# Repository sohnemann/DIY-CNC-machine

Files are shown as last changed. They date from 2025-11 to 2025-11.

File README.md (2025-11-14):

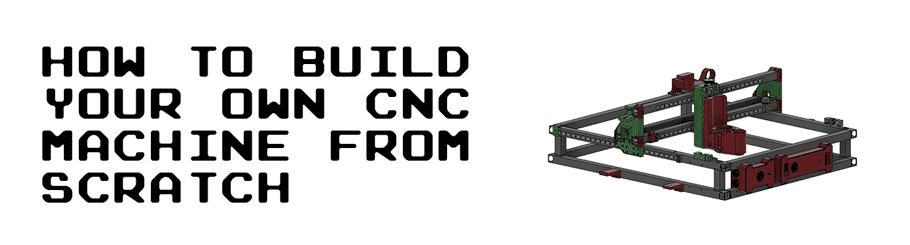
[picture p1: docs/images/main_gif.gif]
main_gif


This guide goes through all the steps to build your own CNC machine from scratch. It includes a complete bill of materials (BOM), STL/OBJ-files for all the 3d-printed parts and detailed instructions of how everything is assembled. It also includes instructions of how all the necessary open-source softwares are installed.

The guide is based on Ivan Miranada's design and is a complement to Ivan's Youtube-videos:

1. Original video: [https://www.youtube.com/watch?v=_atw3e0nIrg](https://www.youtube.com/watch?v=_atw3e0nIrg)
2. Updates with geared stepper motors etc: [https://www.youtube.com/watch?v=qpjf5D3WngY](https://www.youtube.com/watch?v=qpjf5D3WngY)
3. Updating to metal parts: [https://www.youtube.com/watch?v=RDnGvhdGFEY](https://www.youtube.com/watch?v=RDnGvhdGFEY)

If you have any questions, feel free to contact me on LinkedIn: [https://www.linkedin.com/in/max-fischer-92997281/](https://www.linkedin.com/in/max-fischer-92997281/) 

or

contact

cnc_top_gif

---

**Featured on**

* Hackernews (#2): [https://news.ycombinator.com/item?id=29096954](https://news.ycombinator.com/item?id=29096954)
* Console open-source newsletter: [https://console.substack.com/p/console-83](https://console.substack.com/p/console-83)
* Hackaday's blog: [https://hackaday.com/2021/11/05/diy-cnc-uses-lots-of-3d-printed-parts/](https://hackaday.com/2021/11/05/diy-cnc-uses-lots-of-3d-printed-parts/)
* Hackaday's podcast (~25:30): [https://open.spotify.com/episode/2YuxrVAgbQvVTjcUljJ3rj?si=lkp1L061R7ix6WkA7s1ieA](https://open.spotify.com/episode/2YuxrVAgbQvVTjcUljJ3rj?si=lkp1L061R7ix6WkA7s1ieA)
* Arduino's official blog: [https://blog.arduino.cc/2021/11/03/learn-how-to-build-your-own-massive-3d-printed-cnc-router/](https://blog.arduino.cc/2021/11/03/learn-how-to-build-your-own-massive-3d-printed-cnc-router/)
* Weekly robotics newsletter: [https://weeklyrobotics.com/weekly-robotics-168](https://weeklyrobotics.com/weekly-robotics-168)

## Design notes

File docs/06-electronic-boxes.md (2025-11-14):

# Electronic boxes

Two electronic boxes were attached to the front side of the CNC machine, a large box to encapsulate the power supply and a small box to encapsulate the Arduino and the CNC shield.

## Small electronic box

The small electronic box consisted of 4 parts (**P02**, **P04**, **P13**, **P15**). The two middle parts were clamped together on the front-left side of the frame, closest to the Y-axis cable chain. A finger was used to feel that the two parts were perfectly lined up.

Make sure to have enought space on the left side of the box for the all the stepper motor wires, end-stop wires and router power cable to enter the box (the vertical beam might block if you attach it too far to the left). Also make sure that the two holes are pointing to the left.

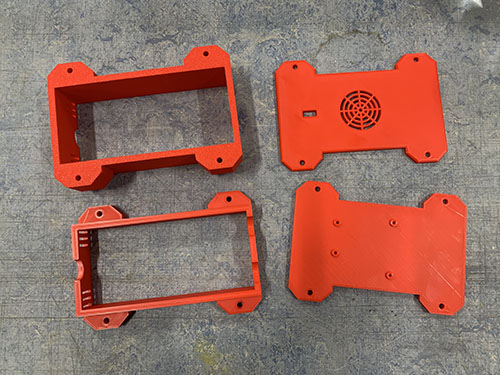
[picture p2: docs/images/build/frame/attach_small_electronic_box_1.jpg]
attach_small_electronic_box_1


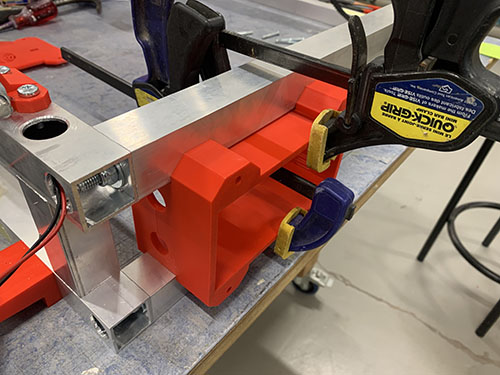
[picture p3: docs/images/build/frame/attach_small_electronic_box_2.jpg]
attach_small_electronic_box_2


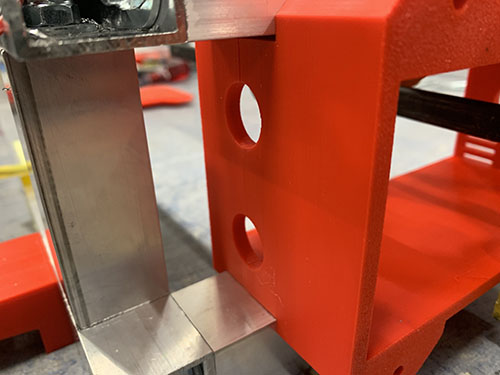
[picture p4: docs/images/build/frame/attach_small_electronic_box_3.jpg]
attach_small_electronic_box_3


The front-middle part (**P13**) was attached first. A small 2 mm drill was used to make indentations at the center of the holes. Cutting fluid was applied and a 3 mm drill was used to drill the holes, followed by a M4 drill tap. The front-middle and front part was then attached to the frame using 4x 40mm M4 screws (**S11**).

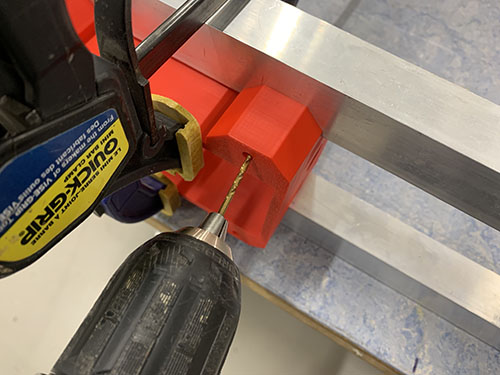
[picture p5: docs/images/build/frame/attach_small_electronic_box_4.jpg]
attach_small_electronic_box_4


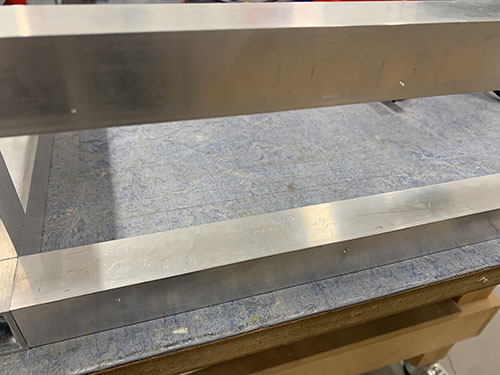
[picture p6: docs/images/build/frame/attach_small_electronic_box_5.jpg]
attach_small_electronic_box_5


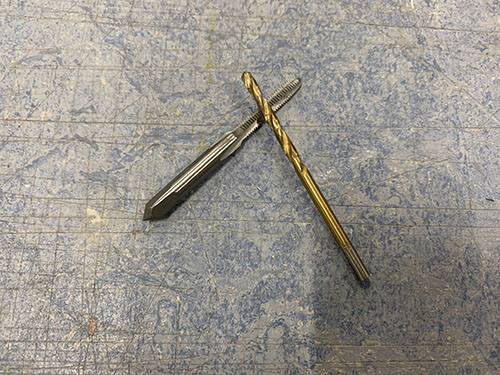
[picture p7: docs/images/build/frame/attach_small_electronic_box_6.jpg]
attach_small_electronic_box_6


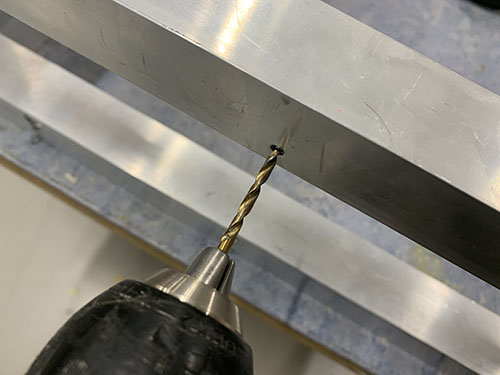
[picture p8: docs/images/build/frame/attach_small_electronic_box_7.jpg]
attach_small_electronic_box_7


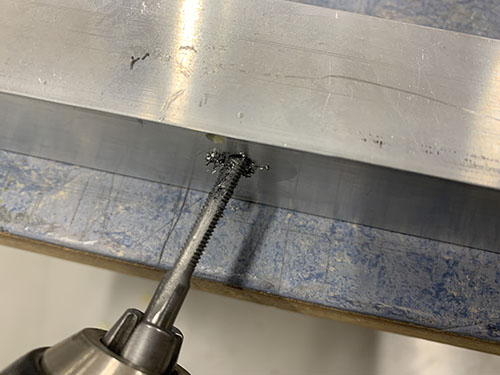
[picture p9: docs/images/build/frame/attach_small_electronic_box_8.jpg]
attach_small_electronic_box_8


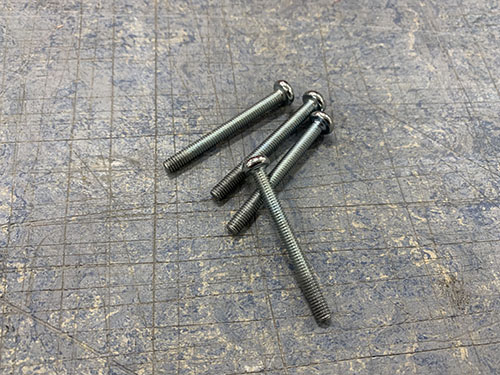
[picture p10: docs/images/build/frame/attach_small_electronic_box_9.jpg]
attach_small_electronic_box_9


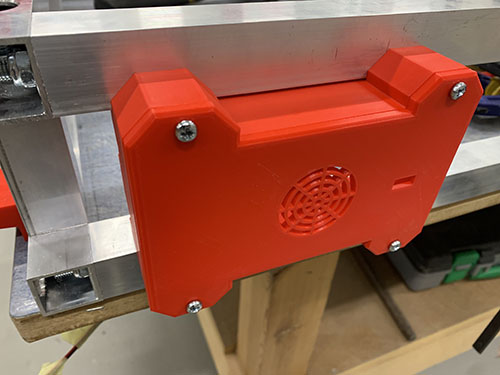
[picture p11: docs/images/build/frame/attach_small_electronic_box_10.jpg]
attach_small_electronic_box_10


To attach the back-middle part (**P02**), the whole CNC machine had to be pushed partly over the edge of the working table to be able to drill on the inside of the frame. The machine was firmly clamped to the table.

The back-middle part was again clamped to the frame and aligned with the now attached front-middle part. A small 2 mm drill was used to make indentations at the center of the holes. Cutting fluid was applied and a 3 mm drill was used to drill the holes, followed by a M4 drill tap. The back-middle and back part was then attached to the frame using 4x 25mm M4 screws (**S10**).

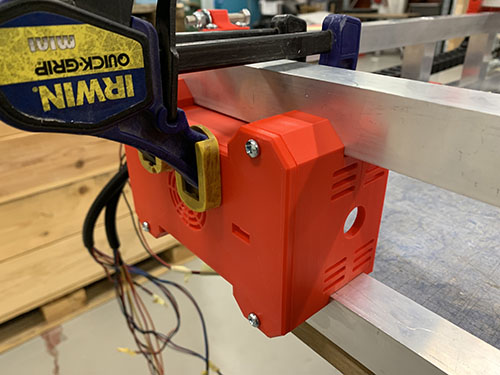
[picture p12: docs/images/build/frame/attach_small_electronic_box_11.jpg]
attach_small_electronic_box_11


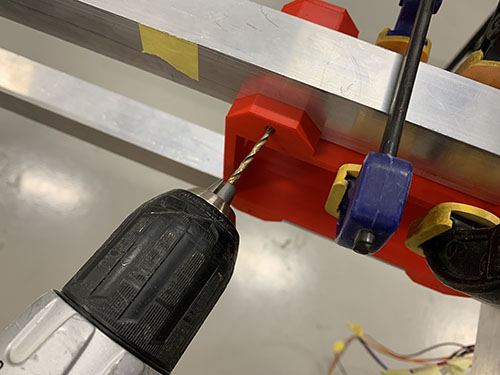
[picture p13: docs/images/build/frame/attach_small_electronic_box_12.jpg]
attach_small_electronic_box_12


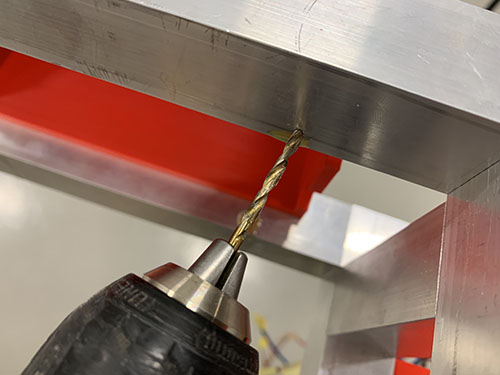
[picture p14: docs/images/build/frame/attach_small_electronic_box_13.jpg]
attach_small_electronic_box_13


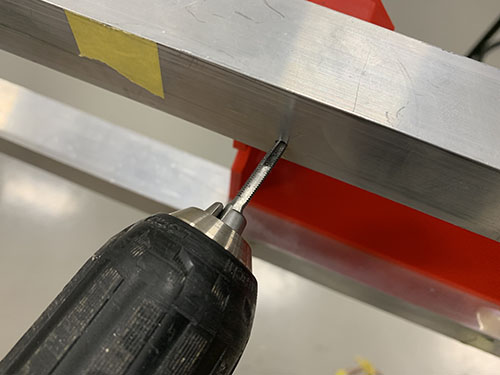
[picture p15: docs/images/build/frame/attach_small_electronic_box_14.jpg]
attach_small_electronic_box_14


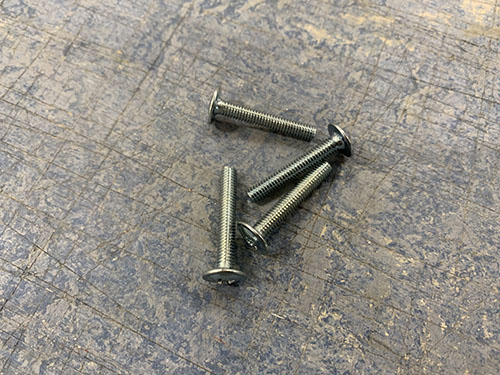
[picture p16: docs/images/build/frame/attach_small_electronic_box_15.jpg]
attach_small_electronic_box_15


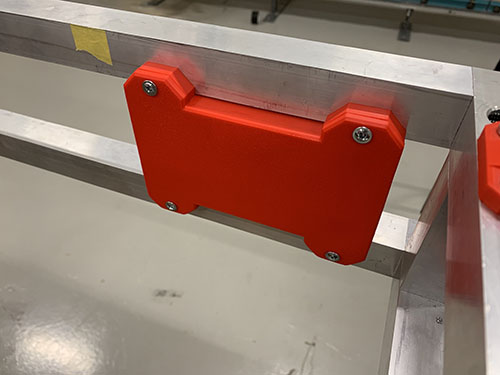
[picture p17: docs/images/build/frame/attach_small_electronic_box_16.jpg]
attach_small_electronic_box_16


## Large electronic box

As the small box, the large electronic box consisted of 4 parts (**P01**, **P03**, **P12**, **P14**). The two middle parts were clamped together to the right of the small box. A finger was used to feel that the two parts were perfectly lined up. 

Make sure that the hole is pointing to the left.

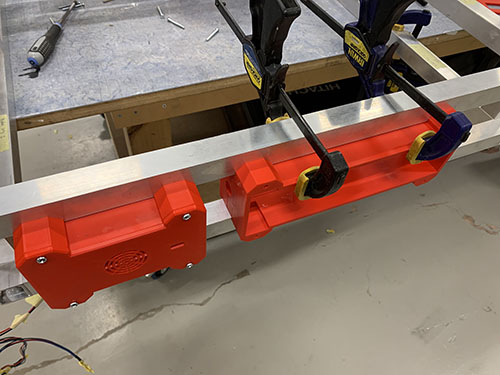
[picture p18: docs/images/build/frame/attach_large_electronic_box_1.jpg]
attach_large_electronic_box_1


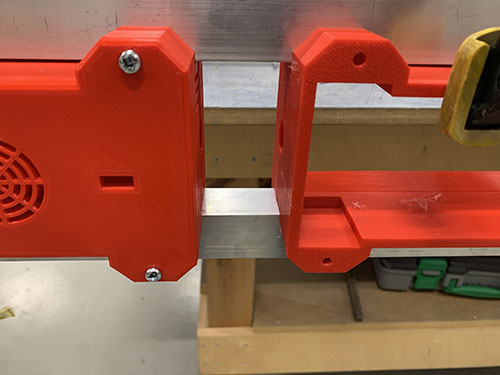
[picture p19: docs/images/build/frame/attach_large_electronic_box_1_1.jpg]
attach_large_electronic_box_1_1


The front-middle part (**P12**) was attached first. A small 2 mm drill was used to make indentations at the center of the holes. Cutting fluid was applied and a 3 mm drill was used to drill the holes, followed by a M4 drill tap. The front-middle and front part was then attached to the frame using 4x 40mm M4 screws (**S11**).

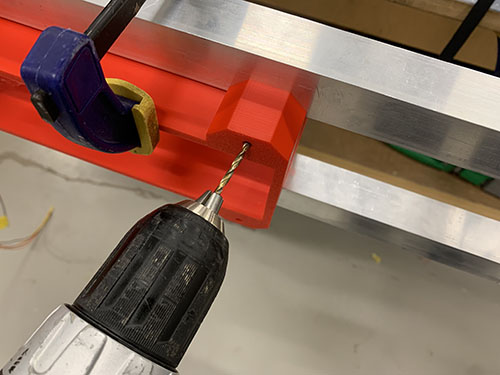
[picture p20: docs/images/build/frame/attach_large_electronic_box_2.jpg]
attach_large_electronic_box_2


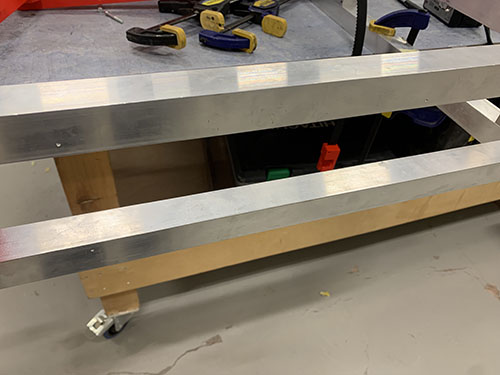
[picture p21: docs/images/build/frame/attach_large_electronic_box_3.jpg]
attach_large_electronic_box_3


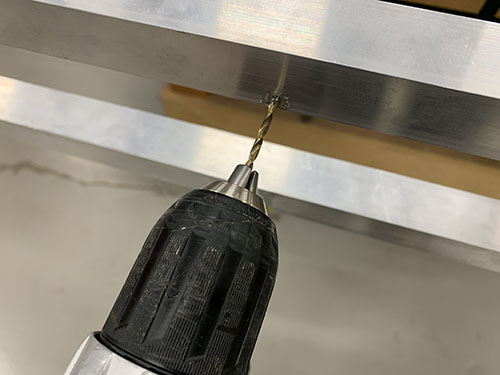
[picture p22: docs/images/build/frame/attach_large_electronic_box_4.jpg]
attach_large_electronic_box_4


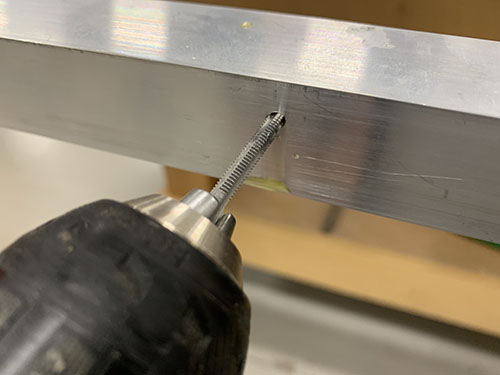
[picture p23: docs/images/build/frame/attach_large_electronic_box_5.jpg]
attach_large_electronic_box_5


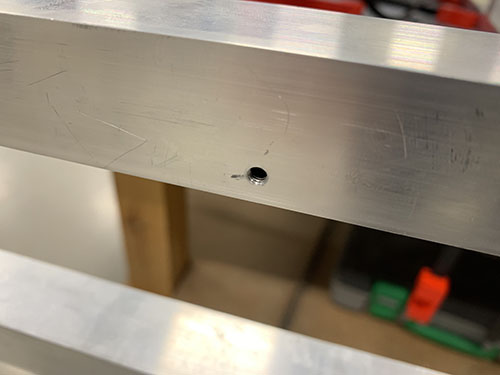
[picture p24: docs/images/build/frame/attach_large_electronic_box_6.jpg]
attach_large_electronic_box_6


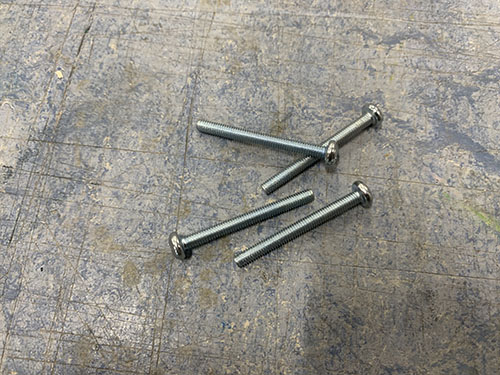
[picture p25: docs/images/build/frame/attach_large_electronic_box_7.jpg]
attach_large_electronic_box_7


attach_large_electronic_box_8

To attach the back-middle part (**P01**), the whole CNC machine had to be pushed partly over the edge of the working table to be able to drill on the inside of the frame. The machine was firmly clamped to the table.

The back-middle part was again clamped to the frame and aligned with the now attached front-middle part. A small 2 mm drill was used to make indentations at the center of the holes. Cutting fluid was applied and a 3 mm drill was used to drill the holes, followed by a M4 drill tap. The back-middle and back part was then attached to the frame using 4x 25mm M4 screws (**S10**).

attach_large_electronic_box_9

attach_large_electronic_box_10

attach_large_electronic_box_11

attach_large_electronic_box_12

attach_large_electronic_box_13

attach_large_electronic_box_14

attach_large_electronic_box_15

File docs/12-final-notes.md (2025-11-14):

# Final notes
I have a couple of things I want to improve with this build:

* [ ] Build a wasteboard using wasteboard clamps
* [x] Design a dust shoe

cnc_top_gif

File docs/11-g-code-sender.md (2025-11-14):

# G-Code sender

To be able to send G-Code instructions from the computer to `grbl` on the Arduino, a G-Code sender is needed. `grbl's` official list of recommended G-Code senders can be found here: [https://github.com/gnea/grbl/wiki/Using-Grbl](https://github.com/gnea/grbl/wiki/Using-Grbl) (Sep 26, 2021)

## Install G-Code sender

In this project a G-code sender called `Universal G-Code Sender (UGS)` was used. The program was downloaded from UGS's official website and the instructions were followed: 

[https://winder.github.io/ugs_website/download/](https://winder.github.io/ugs_website/download/)

After starting the program, you should see something like this:

gcode_sender_1

## Connect G-Code sender to GRBL

To let UGS know where to connect to, the correct firmware (GRBL) and serial port (cu.usbmodem\<NUMBER>) were chosen. If you can't find the correct serial port, click the spinning arrows to refresh the ports.

gcode_sender_2

gcode_sender_3

UGS was then connected to the Arduino by clicking on plug/socket icon in the top left corner. If the connection succeeds, you should see the plug/socket icon turn orange and the GRBL configuration outputted in the console.

gcode_sender_4

gcode_sender_5

## Adjust GRBL configuration

The GRBL configuration enables you to adjust important settings, such as the maximum mm/min rates for different axes and if the end-stops should be used. A full description of all settings can be found here:

[https://github.com/gnea/grbl/blob/master/doc/markdown/settings.md](https://github.com/gnea/grbl/blob/master/doc/markdown/settings.md) (Sep 26, 2021)

To update a setting, the new setting is inputted into the console command line, e.g.: `$21 = 1` to enable end-stops/hard limits. A confirmation that the setting is changed is then outputted in the console.

gcode_sender_6

### Enable end-stops/hard limits

The end-stops/hard limits were enabled by updating the following setting:

`$21 = 0` -> `$21 = 1`

To test that the end-stops were working properly, each end-stop was tested by manually triggering it with a finger. After triggering, an alarm should be raised in UGS.

gcode_sender_7

gcode_sender_8

After the alarm was triggered, UGS was reset by clicking `Soft reset` and `Unlock`.

gcode_sender_9

### Calculate and set travel resolutions

The most important settings to adjust is the X-axis, Y-axis and Z-axis travel resolutions. These settings tells GRBL how many steps it should take to move one millimeter. The travel resolution depends on the stepper motor's steps per revolution, the microstepping, the teeth spacing and the number of teeth on the timing pulley(s).

The following equation was used to calculate the travel resolution (steps/mm) for each stepper:

gcode_sender_10

In this project, this is how the travel resolutions were calculated:

| Stepper motor | Microstepping | Step angle | Steps per revolution | Teeth spacing | Number of teeth - Pulley 1 | Number of teeth - Pulley 2 | Travel resolution |
|---|---|---|---|---|---|---|---|
| X-axis | 16 | 0.094 deg  | 360/0.094 = 3829.7872 steps | 5 mm (HTD**5**M) | 12 | 1 (used when no pulley 2)  | **(16\*3829.7872)/(5\*12/1) = 1021.277** |
| Y-axis (1) | 16 | 0.094 deg  | 360/0.094 = 3829.7872 steps | 5 mm (HTD**5**M) | 12 | 1 (used when no pulley 2)  | **(16\*3829.7872)/(5\*12/1) = 1021.277** |
| Y-axis (2) | 16 | 0.094 deg  | 360/0.094 = 3829.7872 steps | 5 mm (HTD**5**M) | 12 | 1 (used when no pulley 2)  | **(16\*3829.7872)/(5\*12/1) = 1021.277** |
| Z-axis | 16 | 1.8 deg | 360/1.8 = 200 steps | 8 mm (acme rod)  | 16 | 60 | **(16\*200)/(8\*16/60) = 1500** |

The travel resolutions were updated:

* X-axis travel resolution: `$100=250.000` -> `$100 = 1021.277`
* Y-axis travel resolution: `$101=250.000` -> `$101 = 1021.277`
* Z-axis travel resolution: `$102=250.000` -> `$102 = 1500.000`

The calculated travel resolutions were validated by moving each axis 10 mm in UGS and measuring the actual distance moved.

gcode_sender_11

gcode_sender_12

gcode_sender_13

### Other configurations

The homing cycle is when the CNC machine automatically moves all axises to it's limits to home itself before starting the job. I disabled this as I will manually jog the router to it's position:

`$22 = 1` -> `$22 = 0`

The X-axis and Y-axis minimum rates were increased to 1000:

* X-axis maximum rate: `$110=500.000` -> `$110 = 1000.000`
* Y-axis maximum rate: `$111=500.000` -> `$111 = 1000.000`

The X-axis and Y-axis maximum travel were increased to 500:

* X-axis maximum travel: `$130=200.000` -> `$130 = 500.000`
* Y-axis maximum travel: `$131=200.000` -> `$131 = 500.000`

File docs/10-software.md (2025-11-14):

# Software

## Install CNC software (grbl) on Arduino Uno

The software used in this project to control the CNC machine is called `grbl`. It's an open source and high performance g-code-parser and CNC milling controller that can run on a straight Arduino Uno. To be able to install the software on the Arduino, an external computer was needed.

## Install Arduino Software (IDE)
To be able to install `grbl` on the Arduino, `Arduino Software (IDE)` was installed on the computer. This program is used to upload code to the Arduino. The program was downloaded from Arduino's official website and the instructions were followed: 

[https://www.arduino.cc/en/software](https://www.arduino.cc/en/software)

After starting the program, you should see something like this:

install_software_1

## Install GRBL
After installing the Arduino Software, the latest stable version of `grbl` was downloaded (as zip-format) from their official GitHub release page: 

[https://github.com/gnea/grbl/releases](https://github.com/gnea/grbl/releases)

After unzipping the file, you should see something similar to this in the folder:

install_software_2

Before `grbl` was loaded into the `Arduino Software (IDE)`, a minor adjustment had to be done to `grbl's` config file, `config.h`. The reason for this was because when `gbrl` released v1.1, it changed the pin used by the Z end-stops. If this wasn't done, the Z end-stops wouldn't be recognized by `grbl`. To tell `grbl` that the old way of accessing the Z end-stops should be used, a specific variable in the `config.h` was commented out. 

The config `grbl/config.h` was opened in a text editor and the line were the variable `VARIABLE_SPINDLE` is set was commented out by adding two slashes (//) at the beginning of the line (see the last line):

```
// Enables variable spindle output voltage for different RPM values. On the Arduino Uno, the spindle
// enable pin will output 5V for maximum RPM with 256 intermediate levels and 0V when disabled.
// NOTE: IMPORTANT for Arduino Unos! When enabled, the Z-limit pin D11 and spindle enable pin D12 switch!
// The hardware PWM output on pin D11 is required for variable spindle output voltages.
// #define VARIABLE_SPINDLE // <-- THIS SHOULD BE COMMENTED OUT!!
```

The updated `config.h` was saved.

The `Arduino Software (IDE)` was then launched and the `Sketch > Include Library > Add .ZIP Library...` menu alternative was clicked:

install_software_3

You should see a pop-up similar to this:

install_software_4

The unzipped `grbl` directory was opened and the folder `grbl` was chosen. After choosing the folder, a text below the editor appeared stating `Library added to your libraries. Check "Include library" menu`.

A USB cable was connected to the USB connection on the small electronic box.

Next, connect the Arduino to your computer.

install_software_5

To let the IDE know where to upload the software, the correct serial port and board were chosen. The serial port was set under `Tools > Port > SOMETHINGSOMETHING (Arduino Uno)`. 

```
If you have trouble finding the correct port, you might need to install 
CH340 drivers. It might occurr if you're using an Arduino clone. Look at
this resource for more info: 
https://learn.sparkfun.com/tutorials/how-to-install-ch340-drivers/all
```

install_software_8

The board was set under `Tools > Board > Arduino Uno`.

install_software_8_1

To test if the correct board and serial port were chosen, the template code (default code available when launching the IDE) was compiled by clicking on the check mark in the top left corner. When the compiling was done, the right-pointing arrow was clicked to upload the code to the Arduino. If successfull, you should see a text saying `Done uploading` below the editor.

install_software_9

install_software_10

The IDE was now ready to upload `grbl` to the Arduino. This was done by clicking `File > Open` in the top menu:

install_software_11

In the pop-up window, the downloaded folder was found and the following file  `grbl/examples/grblUpload/grblUpload.ino` was opened.

install_software_12

A new pop-up was opened and the `grbl` code was compile by clicking on the check mark. When done, the compiled code was uploaded to the Arduino by clicking on the right-pointing arrow. `grbl` was now installed on the Arduino!

install_software_13

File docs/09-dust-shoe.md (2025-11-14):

# Dust shoe

The purpose of a dust shoe is to collect the dust generated by the CNC machine. Ivan's original dust shoe didn't fit my router, thus I designed a new dust shoe using a brush.

To not have to reprint the router bracket, I manually cut of the blocking piece from it. The STL/OBJ router bracket file in this repo is redesigned and updated, so no manual cutting should be needed.

The brush slot at the bottom of the vaccum funnel (**P34**) was measured and the brush (**O27**) was cut at an appropriate length. The brush was then inserted into the slot. As the fit was very tight, no glue was needed.

dust_shoe_1

dust_shoe_2

dust_shoe_3

dust_shoe_4

The vaccum funnel (**P34**) was placed next to the router bracket (**P24**) and a pen was used to indicate how much of the router bracket that was to be removed.

dust_shoe_5

dust_shoe_6

A hand-held Fein multitool was used to remove the blocking piece from the router bracket. A sand paper was used to smooth out the edges.

dust_shoe_7

dust_shoe_8

dust_shoe_9

dust_shoe_10

The vaccum funnel was then attached to the router bracket and a scissor was used to cut the brush at an appropriate length.

dust_shoe_11

1x 80 mm M5 screw (**S17**) and 1x M5 nut (**N02**) was used to lock the vaccum funnel in place.

dust_shoe_14

dust_shoe_15

dust_shoe_16

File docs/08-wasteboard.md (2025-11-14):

# Wasteboard

## Cut out wasteboard

The length and width of the CNC was measured and a 12 mm plywood (**O26**) was cut out using a vertical panel saw. If you don't have a vertical panel saw, a jigsaw or a circular saw works as well.

wasteboard_1

wasteboard_2

wasteboard_3

## Attach wasteboard to CNC

The wasteboard was placed underneath the CNC machine. 7x 3d-printed wasteboard brackets (**P37**), 14x 3.5x20mm screws (**S01**) and 14x (15mm x 5mm x 1mm) washers (**W02**) were used to to keep the wasteboard in place.

wasteboard_4

wasteboard_5

wasteboard_7

wasteboard_6

wasteboard_8

wasteboard_9

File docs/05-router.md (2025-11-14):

# Router

## Attach router to carriage

A Makita RT0700CJ (**E20**) trimming router was used as I was not able to get my hands on the Makita RT0700C that Ivan is using. To my knowledge, the RT0700CJ is just an upgraded European version of the RT0700C, with the same dimensions.

The trimming router was locked in place by using the router bracket (**P24**), 4x 40mm M5 screws (**S13**), 4x M5 nuts (**N02**) and 4x (10mm x 5mm x 1mm) washers (**W01**).

attach_router_to_carriage_1

attach_router_to_carriage_2

attach_router_to_carriage_3

attach_router_to_carriage_4

attach_router_to_carriage_6

attach_router_to_carriage_7

## Router cable management

**NOTE: THIS PART INCLUDES WIRING OF HIGH VOLTAGE ELECTRICITY THAT CAN BE LETHAL IF NOT DONE PROPERLY. THE COLORS OF THE CABLES CAN VARY DEPENDING ON REGION/COUNTRY AND YOUR COMPONENTS/PINOUT NUMBERS MIGHT LOOK DIFFERENT. BEFORE YOU CONNECT THE POWER CORD TO THE POWER OUTLET, YOU MUST CONSULT WITH A LICENSED ELECTRICIAN TO MAKE SURE THAT EVERYTHING IS PROPERLY WIRED AND THAT IT IS IN LINE WITH YOUR LOCAL LEGISLATIONS.**

To be able to easily replace the trimming router in the future, a power plug (**E04**) and socket were added (**E05**).

router_cable_management_23

First, the router's power cord was cut and stripped at an appropriate length to reach behind the X-axis cable chain mount. A flexible conduit (**O13**) was cut out at an appropriate length and the power cord closest to the router was inserted into the conduit. The end of the power cord and the inside wires were then stripped and twisted.

router_cable_management_1

router_cable_management_2

router_cable_management_3

The power plug was opened up and the wires were connected. The built-in strain relief was then tightened around the cable before the plug was closed again.

router_cable_management_4

router_cable_management_5

router_cable_management_6

router_cable_management_7

router_cable_management_8

The rest of the power cord was inserted through the Y-axis cable chain, around the left side plate (under the cable tie) and through the X-axis cable chain. Getting the power cord through the X-axis cable chain was quite tricky due to the friction of the rubber cable. A cable tie (**O11**) was therefore attached to the top of the cable and used to pull the cable through the cable chain.

router_cable_management_9

router_cable_management_10

router_cable_management_11

router_cable_management_12

router_cable_management_13

router_cable_management_14

router_cable_management_15

The power cord was pulled through the cable chains and adjusted to an appropriate length to reach behind the X-axis cable chain mount. The end of the cable and the inside wires were then stripped and twisted.

router_cable_management_17

router_cable_management_19

The power socket was opened and the wires were attached to the terminals inside. The built-in strain relief was then tightened around the cable before the socket was closed again.

router_cable_management_16

router_cable_management_18

router_cable_management_20

router_cable_management_21

router_cable_management_22

The plug and socket were connected and strapped to the back of the X-axis cable chain mount using cable ties (**O11**). The flexible conduit with the router power cord inside was strapped to the stepper motor flexible conduit using cable ties (**O11**). Make sure that it doesn't touch and drag along the upper bridge beam.

router_cable_management_23

router_cable_management_24

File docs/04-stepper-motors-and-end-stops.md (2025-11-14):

# Stepper motors and end-stops

## Extend stepper motor wires

All 4 stepper motors (2x Y-axis, 1x X-axis and 1x Z-axis) get their power and movement instructions from the Arduino + CNC shield that in a later step will be attached in the small electronic box. Therefore, the stepper motor cables needed to be extended to reach through the cable chains all the way to the front of the machine, where the small electronic box will be located.

AWG22 cables (**E08**) of matching colors were used when increasing the length of the stepper motor cables. The same process was used for all the motors:

1. The amount of wires needed to reach all the way to the electronic box was approximated and cut. Make sure to have an extra ~300 mm wire from the point where the wires exits the Y-axis cable chain, as this will be needed to reach the small electronic box.
2. The ends of the original stepper wires and the extra AWG22 wires were stripped using a wire stripper.
3. The colors of the original stepper wires and the extra AWG22 wires were matched up and the stripped ends of the wires were twisted around each other.
4. The twisted wires where then locked in a steady position by a "third hand".
5. Soldering grease was applied to the twisted wires and the wires were soldered together.
6. 4 shrinking tubes (one per cable) were shrunk around the now soldered twisted wires, covering the soldering.
7. A handful of larger shrinking tubes were shrunk around all 4 wires to keep them together.
8. Finally, the wires were marked using tape and a penn, indicating which stepper motor the wires belonged to. This is important as it will help a lot later on, when the stepper motors are connected to the Arduino.

### Y-axis 1

The extended wires of the first Y-axis stepper motor were cut at a length so that they reached through the lower front bridge beam (see red arrow on the next image) and through the Y-axis cable chain going to the front of the CNC machine.

solder_steppers_y_axis_1

solder_steppers_y_axis_2

solder_steppers_y_axis_3

solder_steppers_y_axis_4

solder_steppers_y_axis_5

solder_steppers_y_axis_6

solder_steppers_y_axis_7

solder_steppers_y_axis_8

solder_steppers_y_axis_9

solder_steppers_y_axis_10

solder_steppers_y_axis_10_1

### Y-axis 2

The extended wires of the second Y-axis stepper motor were cut at a length so that they reached through the Y-axis cable chain going to the front of the CNC machine.

solder_steppers_y_axis_11

solder_steppers_y_axis_12

solder_steppers_y_axis_13

solder_steppers_y_axis_14

solder_steppers_y_axis_15

solder_steppers_y_axis_16

solder_steppers_y_axis_17

solder_steppers_y_axis_18

solder_steppers_y_axis_19

solder_steppers_y_axis_20

### X-axis

I ran out of AWG22 wires when soldering the X-axis stepper motor cables, therefore you will see different type of cables in the upcoming images. Because of this, I had to insert the shrinking tubes before I soldered the cables. Please disregard this and follow the previous instructions.

The extended wire of the X-axis stepper motor were cut at a length so that they reached up and behind the Z-axis stepper motor, through the X-axis cable chain and through the Y-axis cable chain to the front of the CNC machine.

















### Z-axis

The non-geared NEMA17 motor used for the Z-axis had removable wires, in contrast to the 1:19 geared NEMA17 motors that had non-removable wires. The first step was therefore to connect the wires to the NEMA17 motor and cut of the connector on the other side using a scissor. Otherwise, the same procedure was followed as for the other motors.

The extended wires of the Z-axis stepper motor were cut at a length so that they reached through the X-axis cable chain and through the Y-axis cable chain to the front of the CNC machine.





















## End-stops and end-stop wires

End-stops are important, as they do not only enable you to home the CNC machine, but they also limit the CNC machine from moving past what is physically possible. When the end-stops are triggered, an alarm is fired and the machine automatically stops.

The wires used for end-stops were 0.75 mm^2 (**E03**).

### X-axis (max)

A microswitch (**E21**) was attached to the thick X-axis (+) end-stop mount (**P10**) using 2x 12mm M3 screws (**S02**).

attach_endstoppers_x_axis_1

attach_endstoppers_x_axis_2

attach_endstoppers_x_axis_3

attach_endstoppers_x_axis_4

The end-stop mount was then pushed against the backside of the top bridge beam, which enabled the end-stop to trigger on the Z-axis stepper motor. The X-axis (carriage) was then moved to its maximum position and the end-stop mount was positioned in a way so that the end-stop triggered just before the X-axis reached its maximum position.

Please ignore the flexible conduit/hose in the next two images, it will be added in an upcoming step.

attach_endstoppers_x_axis_5

attach_endstoppers_x_axis_7

The end-stop mount was then clamped to the upper bridge beam and a small drill (-2 mm) was used to carefully make indentations at the center of the holes. The end-stop mount was then removed. Cutting fluid was applied and a 4 mm drill was used to drill the holes, followed by a M5 drill tap. The end-stop mount was then attached to the upper bridge beam using 2x 40 mm M5 screws (**S13**).

attach_endstoppers_x_axis_8

attach_endstoppers_x_axis_9

attach_endstoppers_x_axis_10

attach_endstoppers_x_axis_11

attach_endstoppers_x_axis_12

attach_endstoppers_x_axis_13

attach_endstoppers_x_axis_14

attach_endstoppers_x_axis_15

attach_endstoppers_x_axis_16

One black and one red 0.75 mm^2 wire (**E03**) were cut out at a length so that they reached from the X-axis max end-stop to the right side plate, through the top bridge beam and through the Y-axis cable chain to the front of the CNC machine. A handful of shrinking tubes (**O24**) were shrunk around the wires to keep them together.

attach_endstoppers_x_axis_17

attach_endstoppers_x_axis_18

attach_endstoppers_x_axis_19

One end of the wires were taped together and inserted through the upper bridge beam to the side plate on the other side.

attach_endstoppers_x_axis_20

attach_endstoppers_x_axis_21

attach_endstoppers_x_axis_22

A flexible conduit/hose (**O13**) was then cut out and the other side of the cables were inserted through the conduit. The flexible conduit was then inserted ~50 mm into the upper bridge beam and the other side was attached to the outside of the upper bridge beam using cable ties (**O11**).

attach_endstoppers_x_axis_23

attach_endstoppers_x_axis_24

attach_endstoppers_x_axis_25

The end of the wires were stripped and twisted. Two 2.8 mm spade connectors (**E25**) were then attached to the stripped wires using a plier. The red wire was then attached to C (Common terminal) pinout on the end-stop and the black cable was connected to the NO (Normally Open) pinout.

attach_endstoppers_x_axis_26

attach_endstoppers_x_axis_27

attach_endstoppers_x_axis_28

attach_endstoppers_x_axis_29

attach_endstoppers_x_axis_30

Finally, the open end of the wires were marked using tape (**O23**) and a penn, indicating which end-stop the cables belonged to. This is important as it will help a lot later on, when the end-stops are connected to the Arduino.

attach_endstoppers_x_axis_31

### X-axis (min)

A microswitch (**E21**) was attached to the X-axis end-stop (-) mount (**P08**) using 2x 12mm M3 screws (**S02**).

attach_endstoppers_x_axis_32_0

attach_endstoppers_x_axis_32_1

attach_endstoppers_x_axis_32_2

One black and one red 0.75 mm^2 wire (**E03**) were cut out at a length so that they reached from the X-axis end-stop (-), around the left side plate, through the Y-axis cable chain to the front of the CNC machine. A handful of shrinking tubes (**O24**) were shrunk around the wires to keep them together.

attach_endstoppers_x_axis_32

attach_endstoppers_x_axis_33

attach_endstoppers_x_axis_34

The end of the wires were stripped and twisted. Two 2.8 mm spade connectors (**E25**) were then attached to the stripped wires using a plier. The red wire was then attached to C (Common terminal) pinout on the end-stop and the black cable was connected to the NO (Normally Open) pinout.

The wires were initially strapped around the lower front bridge beam (seen in the first two images), but as it turned out it blocked the belt tensioner. So they were instead strapped around the M8 tensioner screw, using a cable tie (**O11**). 

attach_endstoppers_x_axis_36

attach_endstoppers_x_axis_37

attach_endstoppers_x_axis_38

Finally, the open end of the wires were marked using tape and a penn, indicating which end-stop the cables belonged to.

attach_endstoppers_x_axis_39

### Y-axis (max)

The tall Y-axis end-stop (+) mount (**P09**) was clamped to the inner side of the upper frame and a sharpie was used to indicate the center of the holes. Note that this end-stop mount can probably be redesigned to gain an extra ~10 mm of Y-axis movement, something I will probably do in the future.

attach_endstoppers_y_axis_1

attach_endstoppers_y_axis_2

attach_endstoppers_y_axis_3

attach_endstoppers_y_axis_4

A bradawl and a hammer were then used to make indentations at the center of the holes. Cutting fluid was applied and a 4 mm drill was used to drill the holes, followed by a M5 drill tap. The end-stop mount was then attached to the inside of the upper frame using 2x 20 mm M5 screws (**S12**).

attach_endstoppers_y_axis_5

attach_endstoppers_y_axis_6

attach_endstoppers_y_axis_7

attach_endstoppers_y_axis_8

attach_endstoppers_y_axis_9

attach_endstoppers_y_axis_10

attach_endstoppers_y_axis_11

attach_endstoppers_y_axis_12

One black and one red 0.75 mm^2 wire (**E03**) were cut out at a length so that they reached from the Y-axis end-stop (+) and through the 900 mm aluminium profile of the upper frame to the front of the CNC machine.

attach_endstoppers_y_axis_13

attach_endstoppers_y_axis_14

attach_endstoppers_y_axis_15

A microswitch (**E21**) was attached to the tall Y-axis end-stop (+) mount using 2x 12mm M3 screws (**S02**).

attach_endstoppers_y_axis_17

attach_endstoppers_y_axis_18

attach_endstoppers_y_axis_19

A flexible conduit/hose (**O13**) was then cut out and the wires were inserted through the conduit. The flexible conduit was then inserted ~50 mm into the 900 mm aluminium profile of the upper frame. The other side was bent around and attached to the outside of the upper frame using cable ties (**O11**).

attach_endstoppers_y_axis_20

attach_endstoppers_y_axis_21

attach_endstoppers_y_axis_22

The end of the wires were stripped and twisted. Two 2.8 mm spade connectors (**E25**) were then attached to the stripped wires using a plier. The red wire was then attached to C (Common terminal) pinout on the end-stop and the black cable was connected to the NO (Normally Open) pinout.

attach_endstoppers_y_axis_23

attach_endstoppers_y_axis_24

Finally, the open end of the wires were marked using tape and a penn, indicating which end-stop the cables belonged to.

attach_endstoppers_y_axis_16

### Y-axis (min)

A microswitch (**E21**) was attached to the Y-axis end-stop (-) mount (**P08**) using 2x 12mm M3 screws (**S02**).

attach_endstoppers_y_axis_25

attach_endstoppers_y_axis_26

attach_endstoppers_y_axis_27

One black and one red 0.75 mm^2 wire (**E03**) were cut out at a length so that they reached from the Y-axis end-stop (-) and to the front of the CNC machine.

The end of the wires were stripped and twisted. Two 2.8 mm spade connectors (**E25**) were then attached to the stripped wires using a plier. The red wire were then attached to C (Common terminal) pinout on the end-stop and the black cable was connected to the NO (Normally Open) pinout.

attach_endstoppers_y_axis_28

attach_endstoppers_y_axis_29

attach_endstoppers_y_axis_30

attach_endstoppers_y_axis_31

A flexible conduit/hose (**O13**) was cut out and the wires were inserted through the conduit. The flexible conduit was attached to the outside of the upper frame using cable ties (**O11**).

attach_endstoppers_y_axis_33

attach_endstoppers_y_axis_34

attach_endstoppers_y_axis_32

attach_endstoppers_y_axis_35

Finally, the open end of the wires were marked using tape and a penn, indicating which end-stop the cables belonged to.

### Z-axis (max)

The main purpose of the Z-axis end-stop (+) is, apart from homing the machine, to limit the CNC machine from moving past what the length of the rails allow. As the MGN12H blocks contains a lot of small bearing balls, there's a high risk of them falling out if the blocks move past the rail.

To reduce the complexity and amount of wires, I chose not to include a Z-axis end-stop (-), as you are likely to mill straight through your waste board before there's a risk of moving past the Z-axis min limit. But if you want to add a Z-axis min end-stop, just repeat the process in this section with the new switch flipped around.

First, the vertical carriage slider was moved upwards to its maximum point, where the MGN12H blocks are just about to move past the limit of the rails. The Z-axis end-stop trigger (**P39**) was then pressed against the outside of the vertical carriage slider and a sharpie was used to mark the center of the holes.

attach_endstoppers_z_axis_1

attach_endstoppers_z_axis_2

attach_endstoppers_z_axis_3

A 2.5 mm drill was used to drill the holes into the vertical carriage slider. A tip is to mark the drill depth needed using tape. The Z-axis end-stop trigger was then attached to the vertical carriage slider using 2x 12 mm M3 screws (**S02**).

attach_endstoppers_z_axis_4

attach_endstoppers_z_axis_5

attach_endstoppers_z_axis_6

attach_endstoppers_z_axis_7

A microswitch (**E21**) was pressed against the carriage and positioned and aligned to be triggered by the maximum state of the Z-axis end-stop trigger.

attach_endstoppers_z_axis_8

attach_endstoppers_z_axis_9

A 2.5 mm drill was used to drill the first hole into the carriage and the microswitch was attached to the carriage using 1x 12 mm M3 screw (**S02**). After the microswitch was locked into position, the second hole was drilled and the second 12 mm M3 screw (**S02**) was attached.

attach_endstoppers_z_axis_10

attach_endstoppers_z_axis_11

attach_endstoppers_z_axis_12

One black and one red 0.75 mm^2 wire (**E03**) were cut at a length so that they reached over the top bridge beam, through the X-axis cable chain and through the Y-axis cable chain to the front of the CNC machine. A handful of shrinking tubes (**O24**) were shrunk around the wires to keep them together.

attach_endstoppers_z_axis_13

attach_endstoppers_z_axis_14

attach_endstoppers_z_axis_15

The end of the wires were stripped and twisted. Two 2.8 mm spade connectors (**E25**) were then attached to the stripped wires using a plier. The red wire was then attached to C (Common terminal) pinout on the end-stop and the black wire was connected to the NO (Normally Open) pinout.

attach_endstoppers_z_axis_16

attach_endstoppers_z_axis_17

attach_endstoppers_z_axis_18

The wires were strapped around the M8 screw keeping the Z motor mount attached to the carriage, using a cable tie (**O11**).

Finally, the open end of the wires were marked using tape and a penn, indicating which end-stop the cables belonged to.

attach_endstoppers_z_axis_19

attach_endstoppers_z_axis_20

## Stepper motor and end-stop cable management

To keep a nice structure of all the wires, braided cable sleeves (**O08**) and flexible conduits/hoses (**O13**) were used.

### Y-axis steppers and X-axis end-stops

First, the wires from the right-side Y-axis stepper motor were inserted into a small flexible conduit and pushed through the lower bridge beam closest to the carriage.

stepper_motor_cable_management_1

stepper_motor_cable_management_3

stepper_motor_cable_management_4

The wires from the two geared Y-axis stepper motors and the two X-axis end-stops were bundled together into the same cable sleeve. 

stepper_motor_cable_management_6

stepper_motor_cable_management_6_1

stepper_motor_cable_management_6_2

stepper_motor_cable_management_5

stepper_motor_cable_management_6_3

To simplify pushing the wires and the cable sleeve through the cable chain, the wires were taped together, leaving no loose ends to get stuck in the cable chain. This was needed as the wires were longer than the cable sleeve (to reach all the way to the small electronic box in the front of the CNC machine).

A cable tie (**O11**) was used to close the entrence of the cable sleeve.

stepper_motor_cable_management_6_4

stepper_motor_cable_management_6_5

stepper_motor_cable_management_6_6

### X-axis stepper, Z-axis stepper and Z-axis end-stop

First, the wires from the X-axis stepper motor were inserted into a flexible conduit (**O13**). The conduit was then bent over the upper bridge beam, strapped to the vaccum mount and Z motor mount, and then pushed behind the Z-axis stepper motor.

stepper_motor_cable_management_9

stepper_motor_cable_management_10

stepper_motor_cable_management_11

stepper_motor_cable_management_12

The wires from the X-axis stepper, Z-axis stepper and the Z-axis end-stop were bundled together into the same cable sleeve. The cable sleeve was cut at a length so that it reached through the X-axis cable chain, around the left side-plate and through the Y-axis cable chain.

To simplify pushing the wires through the cable chains, the wires were taped together, leaving no loose ends to get stuck in the cable chains. This was needed as the wires were longer than the cable sleeve (to reach all the way to the small electronic box in the front of the CNC machine).

A cable tie (**O11**) was used to close the entrence of the cable sock.

stepper_motor_cable_management_13

stepper_motor_cable_management_13_1

stepper_motor_cable_management_13_2

stepper_motor_cable_management_13_3

stepper_motor_cable_management_13_4

stepper_motor_cable_management_13_5

stepper_motor_cable_management_13_6

stepper_motor_cable_management_13_7

stepper_motor_cable_management_13_8

A cable tie (**O11**) was used to strap the cable sleeve to the left side-plate.

stepper_motor_cable_management_13_9

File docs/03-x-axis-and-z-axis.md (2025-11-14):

# X-axis and Z-axis

## Rails to bridge beams

The last two 600 mm MGN12H rails (**O21**) were attached to two of the 803 mm aluminium bridge beams (**O05**, used for the X-axis). First, the MGN12H blocks (**O22**) were carefully removed from the rails.

attach_rails_to_beams_1

attach_rails_to_beams_2

The same 100 mm distance used to align the belt tension sliders were used to align the rails. Because they will be off center by 3 mm, make sure that you later attach the bridge beams to the side plates in a way so the rails line up. 

The same 3d-printed support tools (**P25**) used to align the rails on the 900 mm aluminium profiles were used here as well. Everything was clamped into position. A bradawl and a hammer were used to make indentations and a 2 mm drill and a M3 drill tap was used to make the screw holes.

attach_rails_to_beams_3

attach_rails_to_beams_4

attach_rails_to_beams_5

attach_rails_to_beams_6

attach_rails_to_beams_7

attach_rails_to_beams_8

attach_rails_to_beams_9

attach_rails_to_beams_10

attach_rails_to_beams_11

The rails were finally attached using 16 mm M3 screws (**S03**) and the MGN12H  rail blocks (**O22**) were gently slided back onto the rails.

attach_rails_to_beams_12

attach_rails_to_beams_13

attach_rails_to_beams_14

attach_rails_to_beams_15

## X-axis tensioner and end-stop mount to lower bridge beam

The fixed tensioner (**P28**) and end-stop mount (**P08**) were attached to the lower bridge beam in the same fashion as on the 900 mm aluminium profiles, using 4x 20mm M5 screws (**S12**). When aligning the fixed tensioner, make sure that the "belt opening" is pointing in the direction of the rail. A bradawl and a hammer were used to make indentations at the center of the holes. Cutting fluid was applied and a 4 mm drill was used to drill the holes, followed by a M5 drill tap.

attach_tensioners_to_beams_1

attach_tensioners_to_beams_2

attach_tensioners_to_beams_3

attach_tensioners_to_beams_4

attach_tensioners_to_beams_5

attach_tensioners_to_beams_6

attach_tensioners_to_beams_7

attach_tensioners_to_beams_8

attach_tensioners_to_beams_9

attach_tensioners_to_beams_10

attach_tensioners_to_beams_11

attach_tensioners_to_beams_12

## Bridge beams to side plates

All three bridge beams (**O05**) were then inserted into the slots on the side plates. Make sure that the two beams with the rails are on top of each other, with the rails pointing outwards. Also, make sure that you insert them in the correct orientation, so that the rails are lined up (due to the rails being 3 mm off center).

attach_beams_to_side_plates_1

attach_beams_to_side_plates_1

attach_beams_to_side_plates_1

attach_beams_to_side_plates_1

When the bridge beams were aligned, the blocker clips (**P21**, **P22**, **P23**, **P30**, **P31**, **P32**) were placed in their correct place and a sharpie was used to mark the center of the holes to be drilled. Similar to before, a bradawl and a hammer were used to make indentations at the center of the holes.

attach_beams_to_side_plates_1

attach_beams_to_side_plates_1

attach_beams_to_side_plates_1

attach_beams_to_side_plates_1

A 7 mm drill bit was used to drill the holes. As these holes were going straight through the profiles, a bench drill was used for precision. A metal file was used to remove all excess metal around the holes.

attach_beams_to_side_plates_1

attach_beams_to_side_plates_1

The bridge beams were then inserted into the slots on the side plates once more, along with all the blocker clips. 2x 140 mm threaded M5 rod (**T01**) was inserted through the bottom two beams and 2x 60 mm M5 (**S14**) screws was inserted through the top bridge beam. It was all tightened using M5 nuts (**N02**).

attach_beams_to_side_plates_1

attach_beams_to_side_plates_1

attach_beams_to_side_plates_1

attach_beams_to_side_plates_1

attach_beams_to_side_plates_1

attach_beams_to_side_plates_1

attach_beams_to_side_plates_1

## Rod bearings to carriage

Before attaching the carriage (**P07**) to the bridge beams, two KFL08 rod bearings (**O19**) were attached on the top and the bottom of the carriage (inside) using 4x 20 mm M5 screws (**S12**) and 4x M5 nuts (**N02**). A tip is to temporarily use the acme rod (used in an upcoming step) to vertically align the two bearings.

assemble_carriage_1

assemble_carriage_2

assemble_carriage_3

assemble_carriage_4

assemble_carriage_5

## Carriage to bridge beams

The carriage was attached to the 4x MGN12H blocks (**O22**) on the bridge beams, using 16x 25 mm M3 screws (**S05**).

attach_carriage_to_beams_1

attach_carriage_to_beams_2

attach_carriage_to_beams_3

attach_carriage_to_beams_4

## X-axis motor, idlers and pulley to carriage

Each idler were made up out of 1x 60 mm fully threaded M8 screw (**S15**), 3x 698zz bearings (**O01**) and 4x (15 mm x 8.5 mm x 1.5mm) washers (**W03**) (1 closest to the idler blocker and 3 closest to the side plate). 2x idlers were then attached to each side plate using 2x M8 nuts (**N03**). Make sure that the bearings are spinning freely.

attach_side_plate_motors_1

attach_side_plate_motors_2

As I designed and added the idler blocker later on in the build, some of the images doesn't have it and they also have 3 washers instead of 1 washer closest to the screw head. I left these images anyways in the guide so you can see how it looks when you attach the idlers, but please ignore the wrong number of washers. Also ignore all the other things around the idlers in the upcoming image, they are taken later on in the build.

attach_idlers_motor_to_carriage_3

Should be idler blockers and a different number of washers in the upcoming images.

attach_idlers_motor_to_carriage_3

attach_idlers_motor_to_carriage_4

attach_idlers_motor_to_carriage_5

To attach the stepper motor to the carriage, the 4x M3 screws locking the gear box to the motor were removed.

attach_idlers_motor_to_carriage_6

attach_idlers_motor_to_carriage_7

attach_idlers_motor_to_carriage_8

The stepper motor was then inserted into the large hole on the carriage, facing towards the bridge beams/idlers. 4x 40 mm M3 screws (**S06**) and 4x M3 washers (**W05**) were used to lock the stepper motor onto the carriage. The motor should be attached so that the cables are facing upwards.

attach_idlers_motor_to_carriage_9

attach_idlers_motor_to_carriage_10

attach_idlers_motor_to_carriage_11

1x HTD5M timing pulley (**O18**) was attached to the motor shaft using set screws.

attach_idlers_motor_to_carriage_12

attach_idlers_motor_to_carriage_13

## X-axis HTD5M belt

The HTD5M belt (**O17**) was first inserted into the fixed belt tensioner using a flat screw driver. It was then stretched along the aluminium profile, below the first idler, around the timing pulley, below the second idler and all the way to the other side.

The belt was cut at an appropriate length and inserted into the belt tensioner (**P27**) using a flat screw driver.

attach_x_axis_belt_1

attach_x_axis_belt_2

attach_x_axis_belt_3

attach_x_axis_belt_4

attach_x_axis_belt_5

The belt tensioner was then attached to the side plate using 1x 60mm fully threaded M8 screw (**S15**), 1x M8 nut (**N03**) and 1x (20mm x 10mm x 2mm) washer (**W04**). The M8 screw in the image is not fully threaded as I lost the one I was suppose to use and had to use another one, so please ignore :)

attach_x_axis_belt_6

attach_x_axis_belt_7

Make sure that the belt is not too loose and not too tight.

attach_x_axis_belt_8

## Acme nut and rails to carriage slider

1x acme nut (**O03**) was inserted from the outside, into the the center hole at the top of the vertical carriage slider (**P36**). It was locked in place using 4x 25mm M3 screws (**S05**).

assemble_carriage_6

assemble_carriage_6

assemble_carriage_7

assemble_carriage_8

2x smaller 200 mm MGN12H rails (**O20**) were then attached to the back of the vertical carriage slider. First, the MGN12H blocks (**O22**) were carefully removed from each rail. After that, the rails were screwed in place on the back of the vertical carriage slider using 16x 20 mm M3 screws (**S04**). The MGN12H blocks were then slided back on and each end were blocked using tape. 

assemble_carriage_9

assemble_carriage_10

assemble_carriage_11

assemble_carriage_12

assemble_carriage_13

## Acme rod and vertical slider to carriage

To attach the vertical slider to the carriage, 16x 25 mm M3 screws (**S05**) were first inserted into the holes on the carriage. You might need to "open up" the holes using a narrow tool (depending on the direction you 3d-printed the carriage).

assemble_carriage_17

assemble_carriage_18

assemble_carriage_19

1x acme rod (**O02**) was then inserted through the two KFL08 rod bearings and the acme nut, and the set screws on the bearings were tightened.

assemble_carriage_14

assemble_carriage_15

assemble_carriage_16

The vertical slider was finally attached to the carriage by attaching the previously mentioned 16x 25 mm M3 screws (**S05**) to the MGN12H blocks on the vertical slider.

assemble_carriage_20

assemble_carriage_21

## Z motor mount and X-axis cable chain

The first step was to find a good length of the X-axis cable chain (**O09**). To simplify this process, the X-axis belt was removed to easier move the carriage along the X-axis.

assemble_carriage_22

The Z motor mount (**P40**) and the X-axis cable chain mount (**P38**) were then attached using 3x 25 mm M4 screws (**S10**), 3x M4 nuts (**N01**) and 3x (10mm x 5mm x 1mm) washers (**W01**).

assemble_carriage_23

assemble_carriage_24

assemble_carriage_25

assemble_carriage_26

assemble_carriage_27

assemble_carriage_28

assemble_carriage_29

assemble_carriage_30

They Z motor mount was then attached to the carriage using 2x 80mm M8 screws (**S16**), 2x M8 nuts (**N03**) and 1x (20mm x 10mm x 2mm) washers (**W04**). The vaccum mount was also inserted and attached to the right-side M8 screw. Please ignore the timing pulley attached to the acme rod in some of the images, it will be attached in a later step.

assemble_carriage_30

assemble_carriage_31

assemble_carriage_32

assemble_carriage_33

assemble_carriage_34

assemble_carriage_35

1x 1 meter cable chain (**O09**) were then clamped to the cable chain mount and to the back-side bridge beam. The carriage was then moved as far to the sides as possible. It's important that the chain doesn't touch any of the side plates when moved. In my case, I had to remove 3 links from the cable chain to get a good length of the chain.

assemble_carriage_36

assemble_carriage_37

assemble_carriage_38

assemble_carriage_39

assemble_carriage_39

The Z motor mount and cable chain mount were then disassembled and the cable chain was properly attached to the cable chain mount using 2x 25mm M4 screws (**S10**), 2x M4 nuts (**N01**) and 2x (10mm x 5mm x 1mm) washers (**W01**).

assemble_carriage_40

assemble_carriage_41

assemble_carriage_42

assemble_carriage_43

The Z motor mount and cable chain mount were then assembled again and attached to the carriage in the same fashion as before.

assemble_carriage_44

assemble_carriage_45

assemble_carriage_46

assemble_carriage_47

The carriage was move all the way to the right side plate and the cable chain was clamped to the lower back bridge beam.

assemble_carriage_48

assemble_carriage_49

A bradawl and a hammer were used to make indentations at the center of the two holes. Cutting fluid was applied and a 3 mm drill was used to drill the holes, followed by a M4 drill tap. The cable chain was then attached to the bridge beam using 2x 25 mm M4 screws (**S10**).

assemble_carriage_50

assemble_carriage_51

assemble_carriage_52

assemble_carriage_53

assemble_carriage_54

assemble_carriage_55

assemble_carriage_56

assemble_carriage_57

assemble_carriage_58

assemble_carriage_59

assemble_carriage_60

Finally, the X-axis belt was reattached and tightened.

assemble_carriage_61

## Y-axis cable chain

The Y-axis cable chain (**O09**) was attached to the frame using 1x cable chain mount (**P05**) and 1x cable chain support (**P06**). The cable chain mount was clamped to the left side of the lower frame and aligned with the last vertial beam. A bradawl and a hammer were used to make indentations at the center of the two holes. Cutting fluid was applied and a 4 mm drill was used to drill the holes, followed by a M5 drill tap. The cable chain mount was then attached to the lower frame using 2x 20 mm M5 screws (**S12**).

assemble_cable_support_y_axis_1

assemble_cable_support_y_axis_2

assemble_cable_support_y_axis_3

assemble_cable_support_y_axis_4

assemble_cable_support_y_axis_5

The cable chain support was only attached to the lower frame for the cable chain to rest on. It was aligned and attached it at the center between the second and third vertical beam. Make sure that it does not go below the bottom frame!

In the same way as the cable chain mount, a bradawl and a hammer were used to make indentations at the center of the two holes. Cutting fluid was applied and a 4 mm drill was used to drill the holes, followed by a M5 drill tap. The support was then attached to the lower frame using 2x 20 mm M5 screws (**S12**).

assemble_cable_support_y_axis_6

assemble_cable_support_y_axis_6

assemble_cable_support_y_axis_7

assemble_cable_support_y_axis_8

assemble_cable_support_y_axis_9

assemble_cable_support_y_axis_10

assemble_cable_support_y_axis_11

The Y-axis cable chain (**O09**) was then attached to the left side plate (**P20**) and lower frame support using 4x 25 mm M4 screws (**S10**), 4x M4 nuts (**N01**) and 4x (10mm x 5mm x 1mm) washers (**W01**).

assemble_cable_support_y_axis_12

assemble_cable_support_y_axis_13

assemble_cable_support_y_axis_14

assemble_cable_support_y_axis_15

assemble_cable_support_y_axis_16

assemble_cable_support_y_axis_17

## Z stepper motor, pulleys and belt

The non-geared NEMA17 stepper motor (**E11**) was attached to the Z-axis motor mount using 4x 8mm M3 screws (**S08**) and 4x M3 washers (**W06**). Make sure that the motor cable connector is pointing in the same direction as the opening of the X-axis cable chain.

1x 16 teeth GT2 timing pulley (**O15**) was then attached to the motor shaft and 1x 60 teeth GT2 timing pulley (**O16**) was attached to the acme rod. Both were locked in place using set screws. Make sure that they line up. 

attach_z_stepper_pulleys_belt_1

attach_z_stepper_pulleys_belt_2

attach_z_stepper_pulleys_belt_3

attach_z_stepper_pulleys_belt_4

attach_z_stepper_pulleys_belt_5

attach_z_stepper_pulleys_belt_6

1x GT2 timing belt (**O14**) was looped around both timing pulleys and stretched. Before tightning the M3 screws and locking the motor into place, make sure that the belt is not too loose and not too tight. 

attach_z_stepper_pulleys_belt_7

attach_z_stepper_pulleys_belt_8

attach_z_stepper_pulleys_belt_9

attach_z_stepper_pulleys_belt_10

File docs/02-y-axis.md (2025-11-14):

# Y-axis

## Side plates to upper frame

Before attaching the side plates, the MGN12H blocks (**O22**) were added back onto the rails, 2x on each side. Be careful when sliding them onto the rails, there are multiple small bearing balls that easily fall out of the blocks.

assemble_side_plates_1

assemble_side_plates_2

The left (**P20**) and right (**P29**) side plates where then attached to the blocks using 16x 20 mm M3 screws (**S04**) (8x on each side plate). Make sure to attach the plates on the correct side (see images below).

I had to redesign the left side plate and reprint it later in the build (after the images were taken). Therefore, the left side plate seen in the upcoming images look a bit different than the one used (see next image for the left side plate used).

assemble_side_plates_3

assemble_side_plates_4

assemble_side_plates_5

assemble_side_plates_6

assemble_side_plates_7

assemble_side_plates_8

## Y-axis motors, idlers and pulleys to side plates

Each idler were made up out of 1x idler blocker (**P16**), 2x 60 mm fully threaded M8 screws (**S15**), 6x 698zz bearings (**O01**) and 8x (15 mm x 8.5 mm x 1.5mm) washers (**W03**) (2x closest to the idler blocker and 6x closest to the side plate). The idlers were then attached to each side plate using two M8 nuts (**N03**). Make sure that the bearings are spinning freely.

attach_side_plate_motors_1

attach_side_plate_motors_2

As I designed and added the idler blocker later on in the build, some of the images doesn't have it and they also have 3x washers instead of 1x washer closest to the screw head. I left these images anyways in the guide so you can see how it looks when you attach the idlers, but please ignore the wrong number of washers. Also ignore all the other things around the idlers in the upcoming 2 images, they are taken later on in the build.

attach_side_plate_motors_3_0

attach_side_plate_motors_3_1

Should be idler blockers and a different number of washers in the upcoming images.

attach_side_plate_motors_3

attach_side_plate_motors_4

attach_side_plate_motors_5

attach_side_plate_motors_6

attach_side_plate_motors_7

To attach the stepper motors to the side plates, the 4x M3 screws (**S07**) locking the gear box to the motor were removed. Save these as they will be used later on to attach the power supply and Arduino to the electronic boxes.

attach_side_plate_motors_1

attach_side_plate_motors_1

The 2x geared stepper motors (**E18**) were then inserted into the large holes on the side plates, facing inwards. 4x 40 mm M3 screws (**S06**) and 4x M3 washers (**W05**) were used to lock each stepper motor to the side plates (I forgot to add the washers in the images below, therefore they're not visible). The motors should be attached so that the cables are facing in the direction of the two bridge beams (i.e. the longer vertical surface on the side plates).

attach_side_plate_motors_1

attach_side_plate_motors_1

attach_side_plate_motors_1

attach_side_plate_motors_1

attach_side_plate_motors_1

1x HTD5M timing pulley (**O18**) was attached to each motor shaft using set screws.

attach_side_plate_motors_1

attach_side_plate_motors_1

attach_side_plate_motors_1

attach_side_plate_motors_1

## Y-axis belt tensioners and end-stop mounts

2x fixed belt tensioners (**P19**, **P28**) were attached to the longer aluminium profiles of the upper frame using 4x 20mm M5 screws (**S12**) (2x for each fixed belt tensioner). When aligning the fixed belt tensioners, make sure that the "belt opening" is pointing in the direction of the rails (1x fixed belt tensioner for each rail). Also make sure that the fixed belt tensioners are positioned on the correct side of the rail (see images). Similar to before, a bradawl and a hammer were used to make indentations at the center of the holes. Cutting fluid was applied and a 4 mm drill was used to drill the holes, followed by a M5 drill tap.

attach_tensioners_and_belts_12

attach_tensioners_and_belts_13

attach_tensioners_and_belts_14

attach_tensioners_and_belts_15

attach_tensioners_and_belts_16

attach_tensioners_and_belts_17

attach_tensioners_and_belts_18

2x belt tension sliders (**P17**, **P26**) were attached on the opposite side of the fixed belt tensioners, ontop of the aluminium profile, using 4x 20mm M5 screws (**S12**). To get them aligned at the exact same place on both sides, a 100 mm distance was cut out and a flat support was clamped to the inner side of the profile. The same drill and tap size were used as for the fixed belt tensioners (4mm drill, M5 drill tap). Make sure that the belt tension sliders are pointing outwards.

attach_tensioners_and_belts_19

attach_tensioners_and_belts_20

attach_tensioners_and_belts_21

attach_tensioners_and_belts_22

attach_tensioners_and_belts_23

attach_tensioners_and_belts_24

attach_tensioners_and_belts_25

attach_tensioners_and_belts_26

attach_tensioners_and_belts_27

2x end-stop mounts (**P08**) were then attached to the same side as the belt tension sliders using 4x 20mm M5 screws (**S12**), facing outwards and aligned with the rails. The same drill and tap size were used as for the fixed belt tensioners (4mm drill, M5 drill tap).

attach_tensioners_and_belts_1

attach_tensioners_and_belts_2

attach_tensioners_and_belts_3

attach_tensioners_and_belts_4

attach_tensioners_and_belts_5

attach_tensioners_and_belts_6

attach_tensioners_and_belts_7

attach_tensioners_and_belts_8

attach_tensioners_and_belts_9

attach_tensioners_and_belts_10

attach_tensioners_and_belts_11

The belt tensioners (**P18**, **P27**) were loosely attached to the belt tension sliders using 2x 60 mm fully threaded M8 screws (**S15**), 2x M8 nuts(**N03**) and 2x (20mm x 10mm x 2mm) washers (**W04**).

attach_tensioners_and_belts_28

attach_tensioners_and_belts_29

## Y-axis HTD5M belts

The HTD5M belt (**O17**) was first inserted into one of the fixed belt tensioners using a flat screw driver. It was then stretched along the aluminium profile, below the first idler, around the timing pulley, below the second idler and all the way to the belt tensioner.

attach_tensioners_and_belts_30

attach_tensioners_and_belts_31

attach_tensioners_and_belts_32

attach_tensioners_and_belts_33

attach_tensioners_and_belts_34

A scissor was used to cut the belt at an appropriate length. The loose end was then inserted into the belt tensioner using a flat screw driver and the belt was stretched by tightning the M8 nut.

attach_tensioners_and_belts_35

attach_tensioners_and_belts_36

attach_tensioners_and_belts_37

attach_tensioners_and_belts_38

attach_tensioners_and_belts_39

Make sure that the belt is not too loose and not too tight.

attach_tensioners_and_belts_40

attach_tensioners_and_belts_41

Repeat on the other side.

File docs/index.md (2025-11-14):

# DIY-CNC-machine

main_gif

This guide goes through all the steps to build your own CNC machine from scratch. It includes a complete bill of materials (BOM), STL/OBJ-files for all the 3d-printed parts and detailed instructions of how everything is assembled. It also includes instructions of how all the necessary open-source softwares are installed.

The guide is based on Ivan Miranada's design and is a complement to Ivan's Youtube-videos:

1. Original video: [https://www.youtube.com/watch?v=_atw3e0nIrg](https://www.youtube.com/watch?v=_atw3e0nIrg)
2. Updates with geared stepper motors etc: [https://www.youtube.com/watch?v=qpjf5D3WngY](https://www.youtube.com/watch?v=qpjf5D3WngY)
3. Updating to metal parts: [https://www.youtube.com/watch?v=RDnGvhdGFEY](https://www.youtube.com/watch?v=RDnGvhdGFEY)

If you have any questions, feel free to contact me on LinkedIn: [https://www.linkedin.com/in/max-fischer-92997281/](https://www.linkedin.com/in/max-fischer-92997281/) 

or

contact

cnc_top_gif

---

**Featured on**

* Hackernews (#2): [https://news.ycombinator.com/item?id=29096954](https://news.ycombinator.com/item?id=29096954)
* Console open-source newsletter: [https://console.substack.com/p/console-83](https://console.substack.com/p/console-83)
* Hackaday's blog: [https://hackaday.com/2021/11/05/diy-cnc-uses-lots-of-3d-printed-parts/](https://hackaday.com/2021/11/05/diy-cnc-uses-lots-of-3d-printed-parts/)
* Hackaday's podcast (~25:30): [https://open.spotify.com/episode/2YuxrVAgbQvVTjcUljJ3rj?si=lkp1L061R7ix6WkA7s1ieA](https://open.spotify.com/episode/2YuxrVAgbQvVTjcUljJ3rj?si=lkp1L061R7ix6WkA7s1ieA)
* Arduino's official blog: [https://blog.arduino.cc/2021/11/03/learn-how-to-build-your-own-massive-3d-printed-cnc-router/](https://blog.arduino.cc/2021/11/03/learn-how-to-build-your-own-massive-3d-printed-cnc-router/)
* Weekly robotics newsletter: [https://weeklyrobotics.com/weekly-robotics-168](https://weeklyrobotics.com/weekly-robotics-168)

## License
The following license is included when buying Ivan Miranda's blueprints of the CNC machine:

```
Everything that is in these files that I produced myself, apart from reselling the files, is allowed.
You can print and sell parts, sell machines, sell courses to build the machine. Modify the parts and post 
them for free, as long as you don’t sell the files and keep this license on everything you make with the 
files and credit me, we’re good. No DRM or anything, you are even allowed to repost the files as long as 
they’re kept free. Why buy this then? To support me and keep me encouraged to do more projects like this. 
```

Ivan does an amazing job putting these DIY builds together. I've posted his STL-files in this repository to simplify the build, but PLEASE buy his blueprints here: [https://ivanmiranda.com/products/3d-printed-cnc](https://ivanmiranda.com/products/3d-printed-cnc). It's only \$25 and helps him to continue build and share his awesome projects. Also, you will get access to a Discord channel that is really useful, where you can ask questions to a lot of people who have already built the machine.

Also, the Z-axis end-stop trigger, the ordinary end-stops and the rail supports all come from cello4's GitHub: [https://github.com/4cello/mirandacnc-community](https://github.com/4cello/mirandacnc-community).

## Parts (bill of materials)

**CLICK HERE TO OPEN THE BILL OF MATERIALS (BOM) MARKDOWN: [Bill of materials](./BILLOFMATERIAL.md)**

To simplify the build, I've created a separate markdown page with tables covering all parts needed to build the CNC-machine. The tables include a unique `Item No.` to easier refer to the parts in the guide. The tables also include images of all parts and .STL/.OBJ files of the parts that needs to be 3d-printed.

To get an even better understanding of how all the parts are used, I've created a detailed spreadsheet with comments:

* [On Google drive](https://docs.google.com/spreadsheets/d/1VdnPilA22OfAh9a1y4Ft6c2xkio206Dzv85h7AX7CmQ/edit?usp=sharing)
* [Bill\_of\_material.xlsx](./Bill_of_material.xlsx)

**To be able to continue with the build, you need to buy and 3d-print all needed parts found in the [bill of materials](./BILLOFMATERIAL.md).**

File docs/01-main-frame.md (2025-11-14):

# Main frame

## Drill holes in 900 mm profiles
The main frame consists of two separate frames, the lower and the upper frame. The two frames are kept together using threaded rods, washers and nuts. To enable the threaded rods to slide through the aluminium profiles, holes needed to be drilled.

First, a sharpie was used to indicate where all the holes were going in the 900mm profiles (**O07**). This was done by using a set square and a penn. A bradawl and a hammer were then used to make indentations at the center of the holes.

holes_main_frame_1

A 9 mm drill-bit and a bench drill was used to drill the holes straight through the profiles.

holes_main_frame_1

holes_main_frame_1

To be able to access the nuts and tight them with a socket wrench, some holes (facing outwards, see Fusion360 CAD file) needed to be enlarged. A sharpie was used to mark all the holes that needed to be enlarged.

holes_main_frame_1

A step drill was then used to enlarge the holes holes to 20 mm. A tip is to measure the size of your socket wrench and keep the holes as small as possible, while you're still able to tighten the nuts. To be able to see which step you're aiming for on the step drill, attach a small piece of masking tape on the step above.

holes_main_frame_1

holes_main_frame_1

holes_main_frame_1

holes_main_frame_1

The edges were finally smoothed out using a round metal file.

holes_main_frame_1

holes_main_frame_1

holes_main_frame_1

### Rails to 900 mm profiles

Before the upper and lower frames were assembled, two 600 mm MGN12H rails (**O21**) were attached to the 900 mm aluminium profiles (**O07**) of the **upper** frame. They were attached to the sides facing outwards and above the three 80 mm vertical beams (connecting the lower and upper frame). A tip is to place all the profiles as they should go to make sure that you're attaching the rails to the correct faces (see the red boxes on the image below). Also, be very careful when removing the MGN12H blocks (**O22**) from the rails.

attach_rails_to_beams_2

rails_main_frame_1

rails_main_frame_0

3x 3d-printed support tools (**P25**) were used to center the rails on the profiles. A 57 mm wood block were cut out and used to attach the rails at the same distance from the end of the profiles on both sides. The rails were then clamped to the profiles.

rails_main_frame_2

rails_main_frame_3

rails_main_frame_4

rails_main_frame_5

A bradawl and a hammer were then used to make indentations at the center of the holes. Cutting fluid was applied and a 2 mm drill was used to drill all the holes.

rails_main_frame_6

rails_main_frame_7

rails_main_frame_8

rails_main_frame_9

rails_main_frame_10

rails_main_frame_11

Cutting fluid was then applied once more on the drilled holes and a M3 drill tap was used to create threads in the holes.

rails_main_frame_12

rails_main_frame_13

Finally, the rails were attached using 48x 16 mm M3 screws (**S03**).

rails_main_frame_14

rails_main_frame_15

rails_main_frame_16

rails_main_frame_17

## Assemble upper and lower frames

The two frames were assembled using the 4x 717 mm M8 threaded rods (**T03**), 8x (20mm, 10mm, 2mm) washers (**W04**) and 8x M8 lock nuts (**N03**).

The profiles were first placed in their correct place and clamps were used to keep the profiles aligned. I used two jointed spanners (one one each side) to lock everything in place, but you can also use two socket wrenches. Just make sure that the bits fit into the drilled holes.

assemble_frames_1

assemble_frames_3

assemble_frames_2

assemble_frames_4

assemble_frames_5

assemble_frames_6

assemble_frames_7

## Interlock upper and lower frames

The upper and lower frames and the 8x 80 mm vertical aluminium beams (**O06**) were first layed out in their correct place. The 803 mm horizontal bridge beams (used later in the tutorial) (**O05**) and clamps were then used to align the frames on top of each other.

assemble_frames_9

assemble_frames_10

8x 120 mm M8 threaded rods (**T02**), 16x (20mm, 10mm, 2mm) washers (**W04**) and 16x M8 lock nuts (**N03**) were then used to interlock the upper and lower frames, with the 80 mm vertical aluminium profiles in between.

assemble_frames_8

assemble_frames_12

assemble_frames_11

assemble_frames_13

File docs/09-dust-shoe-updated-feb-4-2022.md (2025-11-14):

## Dust shoe (updated Feb 4, 2022)

The purpose of a dust shoe is to collect the dust generated by the CNC machine. Ivan's original dust shoe didn't fit my router, thus I designed a new dust shoe using a brush.

To not have to reprint the router bracket, I manually cut of the blocking piece from it. The STL/OBJ router bracket file in this repo is redesigned and updated, so no manual cutting should be needed.

The brush slot at the bottom of the vaccum funnel (**P34**) was measured and the brush (**O27**) was cut at an appropriate length. The brush was then inserted into the slot. As the fit was very tight, no glue was needed.

dust_shoe_1

dust_shoe_2

dust_shoe_3

dust_shoe_4

The vaccum funnel (**P34**) was placed next to the router bracket (**P24**) and a pen was used to indicate how much of the router bracket that was to be removed.

dust_shoe_5

dust_shoe_6

A hand-held Fein multitool was used to remove the blocking piece from the router bracket. A sand paper was used to smooth out the edges.

dust_shoe_7

dust_shoe_8

dust_shoe_9

dust_shoe_10

The vaccum funnel was then attached to the router bracket and a scissor was used to cut the brush at an appropriate length.

dust_shoe_11

1x 80 mm M5 screw (**S17**) and 1x M5 nut (**N02**) was used to lock the vaccum funnel in place.

dust_shoe_14

dust_shoe_15

dust_shoe_16

# Software

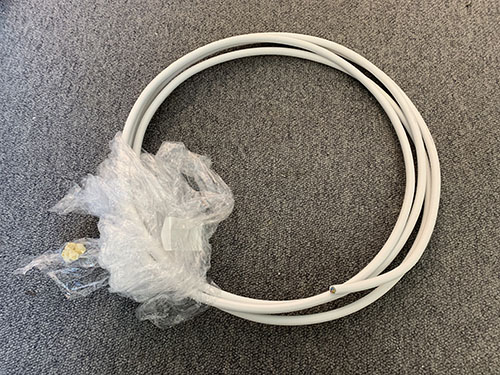
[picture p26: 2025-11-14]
docs/images/parts/electronics/220V_cable.jpg

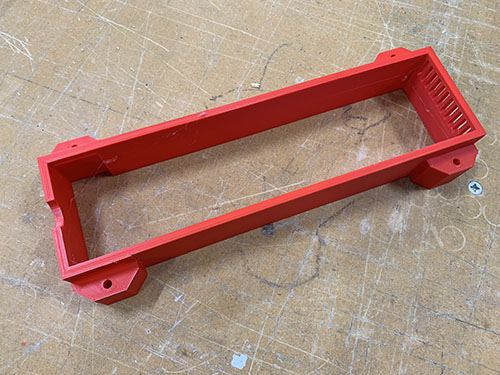
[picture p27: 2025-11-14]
docs/images/3dprinted_parts/electronic_box_large/large_electronic_box_middle_front_panel.jpg

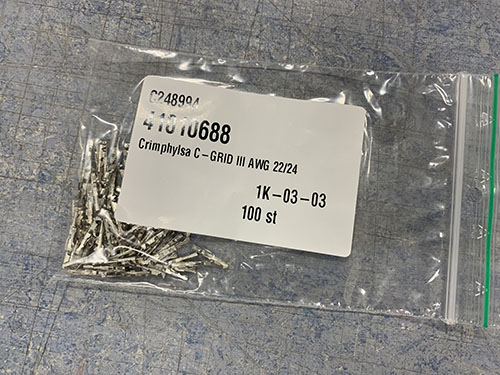
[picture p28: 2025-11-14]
docs/images/parts/electronics/crimp_sleeve.jpg

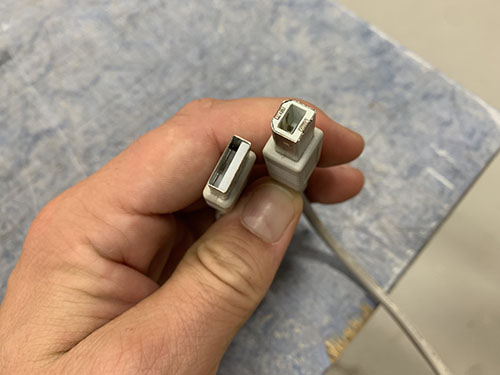
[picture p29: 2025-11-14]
docs/images/parts/electronics/USB_A_to_USB_B.jpg

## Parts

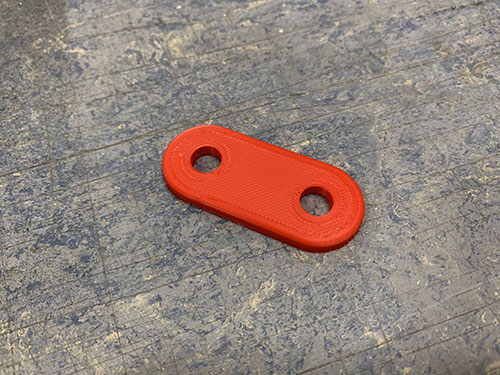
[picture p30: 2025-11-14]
docs/images/3dprinted_parts/other/idler_block.jpg

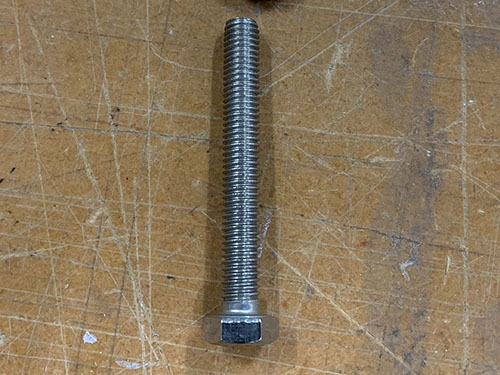
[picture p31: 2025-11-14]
docs/images/parts/consumables/screws/M8/M8_60mm.jpg

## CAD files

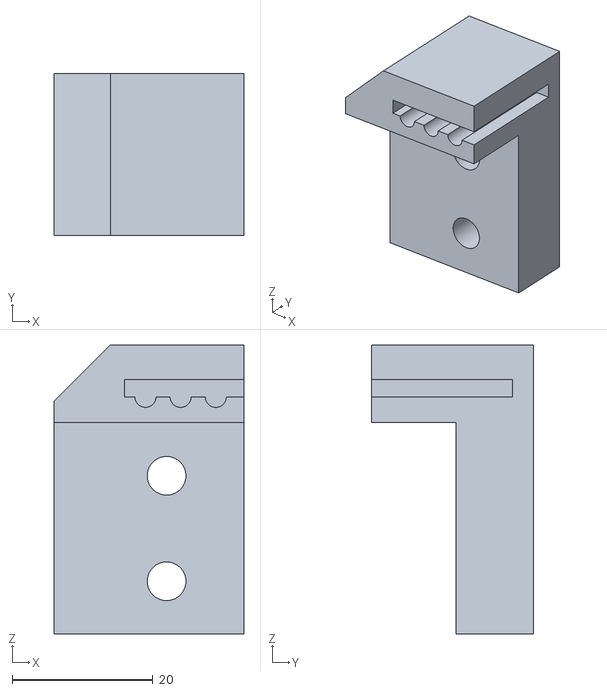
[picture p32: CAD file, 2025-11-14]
docs/stl_files/belt_tensioner/x_axis/X_AXIS_BACK_CLIP.stl
27.0 x 23.0 x 41.1

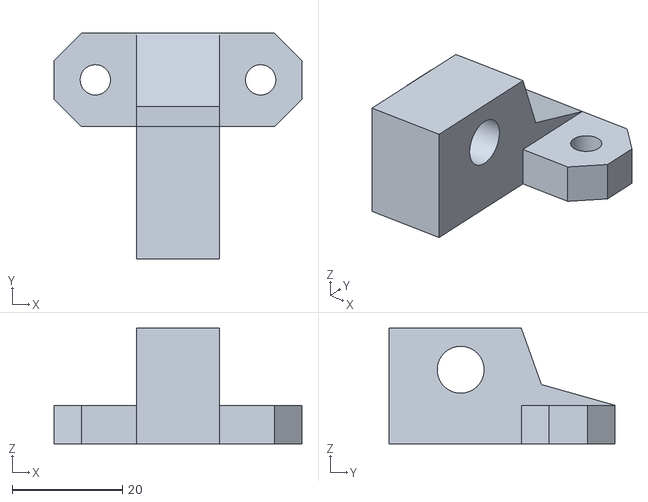
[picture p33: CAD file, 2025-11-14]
docs/stl_files/belt_tensioner/y_axis_left/Y_AXIS_LEFT_BELT_TENSIONER.stl
45.0 x 41.0 x 21.0

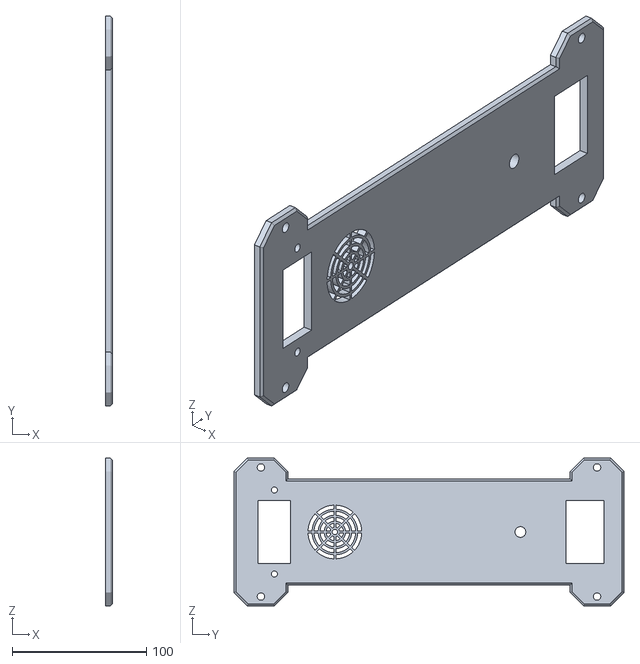
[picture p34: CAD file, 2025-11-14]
docs/stl_files/electronic_box_large/front_panel_electronic_box_large.stl
5.00 x 290.0 x 110.0

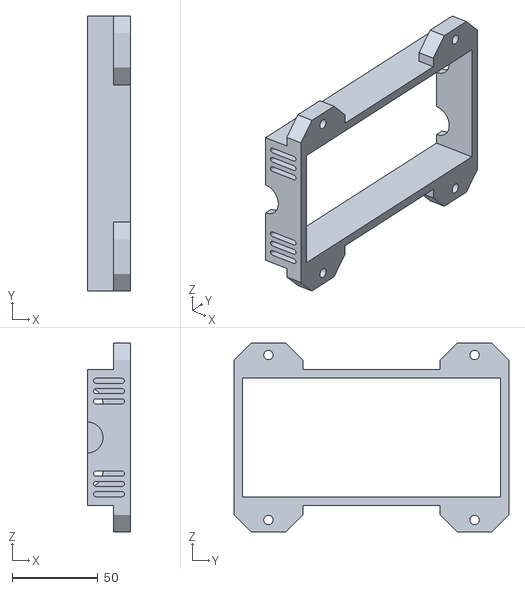
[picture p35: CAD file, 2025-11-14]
docs/stl_files/electronic_box_small/middle_back_panel_electronic_box_small.stl
25.0 x 160.0 x 110.0

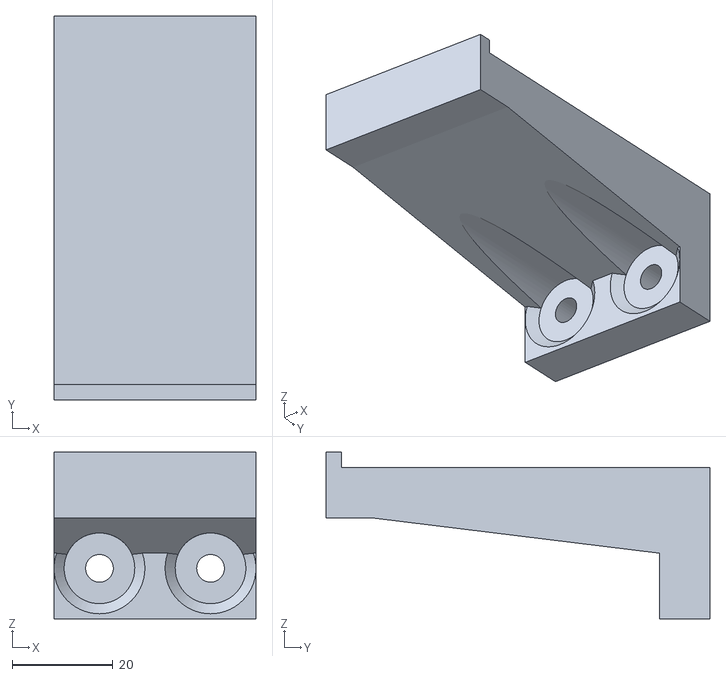
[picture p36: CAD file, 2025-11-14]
docs/stl_files/other/Y_CHAIN_BOTTOM_BRACKET_SUPPORT_2.stl
40.0 x 76.0 x 33.0

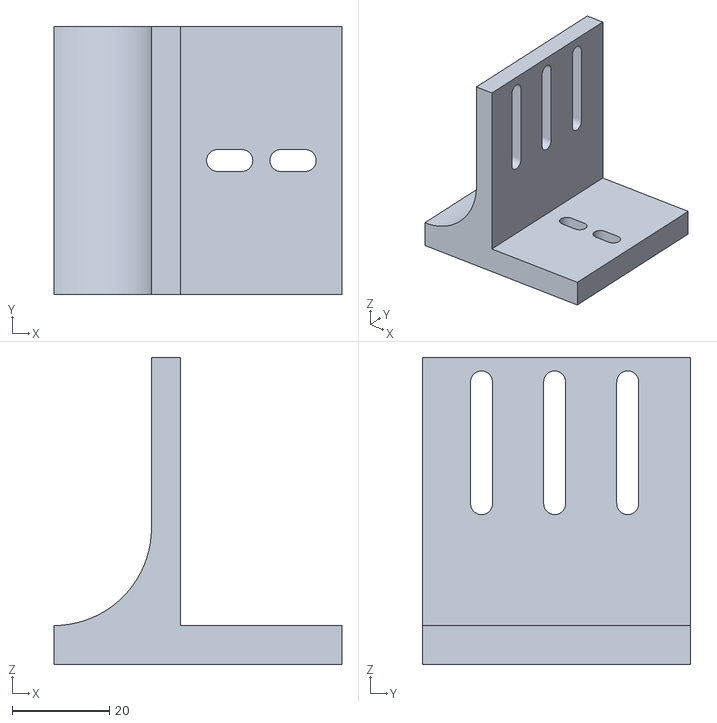
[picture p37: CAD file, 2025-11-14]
docs/stl_files/router/CABLE_CHAIN_MOUNT.stl
59.1 x 55.0 x 63.0

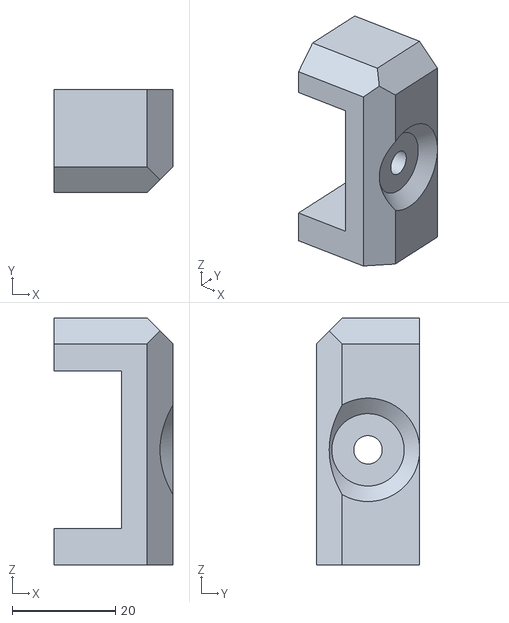
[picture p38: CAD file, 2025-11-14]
docs/stl_files/side_plates/left/LEFT_PLATE_UPPER_FRONT_CLIP.stl
23.0 x 20.0 x 47.8

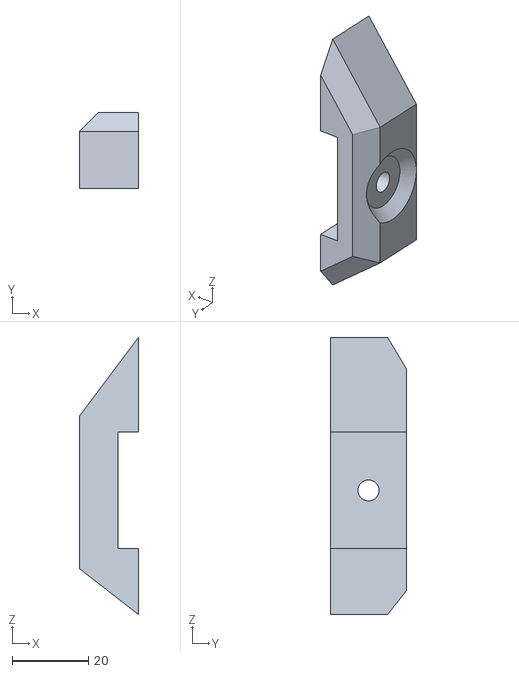
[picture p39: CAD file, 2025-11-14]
docs/stl_files/side_plates/right/RIGHT_PLATE_BACK_CLIP.stl
15.4 x 20.0 x 72.5

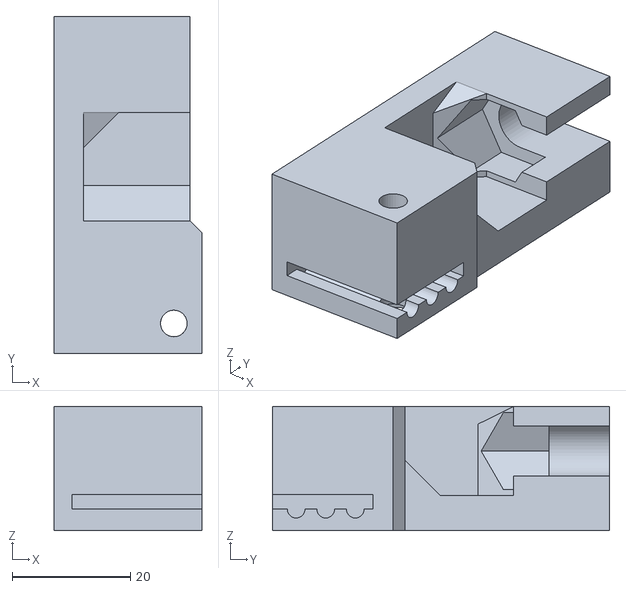
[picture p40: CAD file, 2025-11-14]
docs/stl_files/belt_tensioner/x_axis/X_AXIS_FRONT_CLIP.stl
25.0 x 57.0 x 21.0

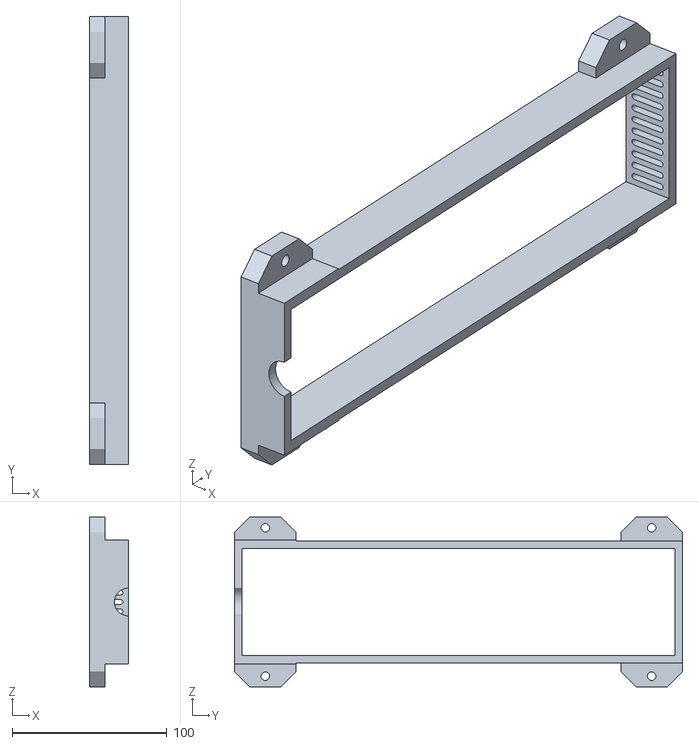
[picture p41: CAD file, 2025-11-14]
docs/stl_files/electronic_box_large/middle_back_panel_electronic_box_large.stl
25.0 x 290.0 x 110.0

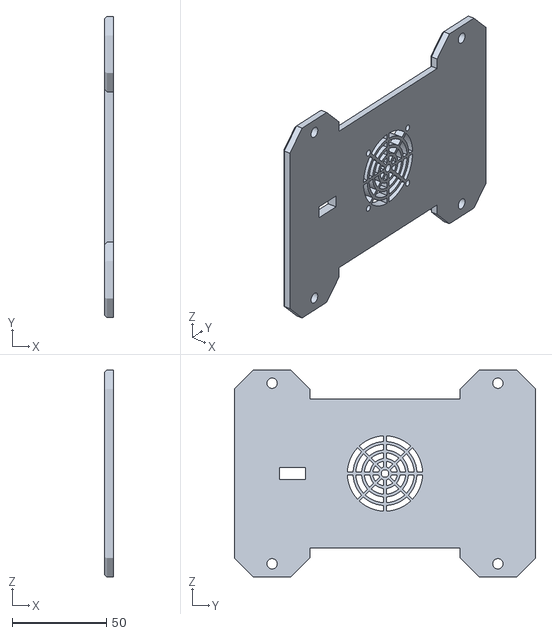
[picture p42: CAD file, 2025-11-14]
docs/stl_files/electronic_box_small/front_panel_electronic_box_small.stl
5.00 x 160.0 x 110.0

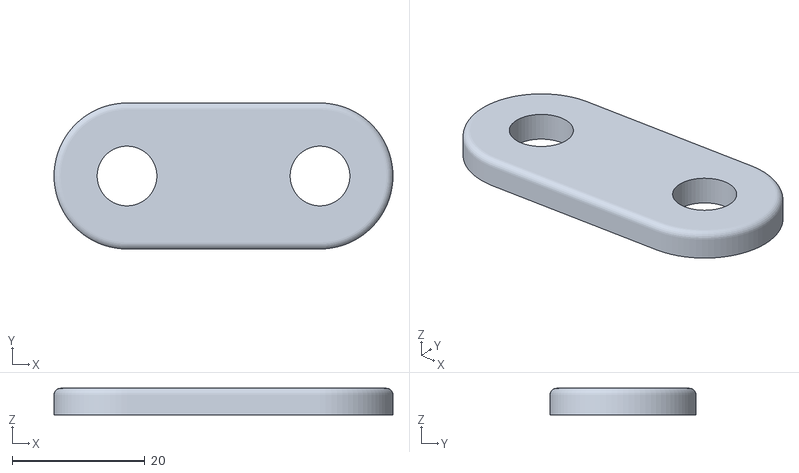
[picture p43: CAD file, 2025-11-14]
docs/stl_files/other/IDLER_BLOCK.stl
51.1 x 22.0 x 4.00

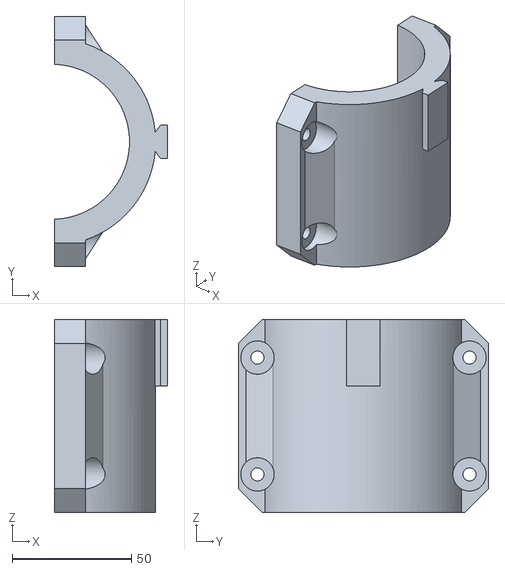
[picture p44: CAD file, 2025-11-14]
docs/stl_files/router/ROUTER_BRACKET.stl
47.5 x 105.0 x 81.0

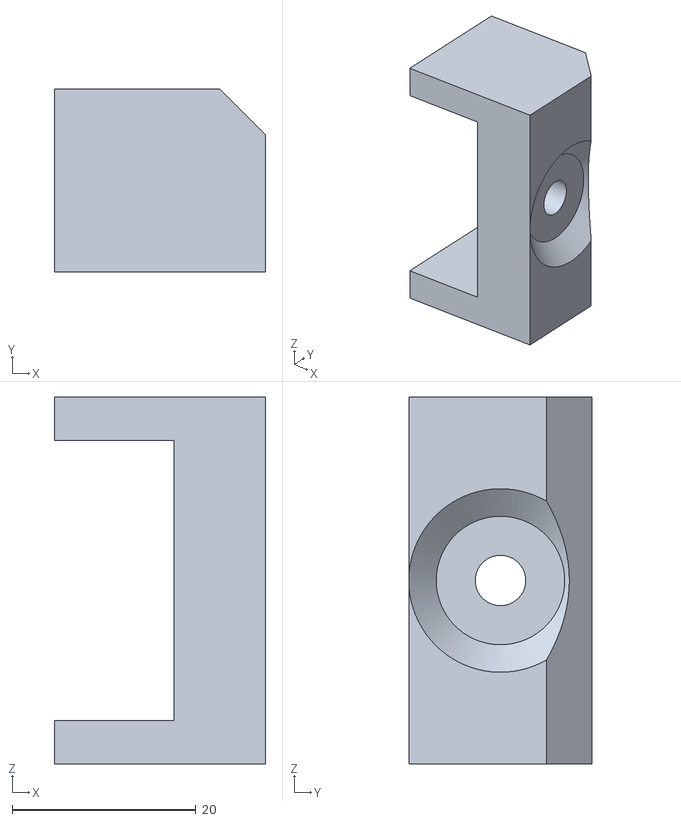
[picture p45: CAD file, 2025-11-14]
docs/stl_files/side_plates/right/RIGHT_PLATE_LOWER_FRONT_CLIP.stl
23.0 x 20.0 x 40.0

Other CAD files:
docs/stl_files/belt_tensioner/y_axis_left/Y_AXIS_LEFT_BACK_CLIP.stl
docs/stl_files/belt_tensioner/y_axis_right/Y_AXIS_RIGHT_BELT_TENSIONER.stl
docs/stl_files/side_plates/left/LEFT_PLATE_BACK_CLIP.stl
docs/obj_files/belt_tensioner/x_axis/X_AXIS_BACK_CLIP.obj
docs/obj_files/belt_tensioner/x_axis/X_AXIS_FRONT_CLIP.obj
docs/obj_files/belt_tensioner/y_axis_left/Y_AXIS_LEFT_BACK_CLIP.obj
docs/obj_files/belt_tensioner/y_axis_left/Y_AXIS_LEFT_BELT_TENSIONER.obj
docs/obj_files/belt_tensioner/y_axis_left/Y_AXIS_LEFT_FRONT_CLIP.obj
docs/obj_files/belt_tensioner/y_axis_right/Y_AXIS_RIGHT_BACK_CLIP.obj
docs/obj_files/belt_tensioner/y_axis_right/Y_AXIS_RIGHT_BELT_TENSIONER.obj
docs/obj_files/belt_tensioner/y_axis_right/Y_AXIS_RIGHT_FRONT_CLIP.obj
docs/obj_files/electronic_box_large/back_panel_electronic_box_large.obj
docs/obj_files/electronic_box_large/front_panel_electronic_box_large.obj
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

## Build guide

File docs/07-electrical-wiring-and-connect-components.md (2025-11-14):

# Electrical wiring and connect components

## Main power supply

!!! danger
    **THIS PART INCLUDES WIRING OF HIGH VOLTAGE ELECTRICITY THAT CAN BE LETHAL IF NOT DONE PROPERLY. THE COLORS OF THE CABLES CAN VARY DEPENDING ON REGION/COUNTRY AND YOUR COMPONENTS/PINOUT NUMBERS MIGHT LOOK DIFFERENT. BEFORE      YOU CONNECT THE POWER CORD TO THE POWER OUTLET, YOU MUST CONSULT WITH A LICENSED ELECTRICIAN TO MAKE SURE THAT EVERYTHING IS PROPERLY WIRED AND THAT IT IS IN LINE WITH YOUR LOCAL LEGISLATIONS.**

The large electronic box was detached from the frame.

The 200W power supply (**E02**) was then attached to the back panel of the larger electronic box using 4x 5mm M3 screws (**S07**) unscrewed from the geared stepper motors.

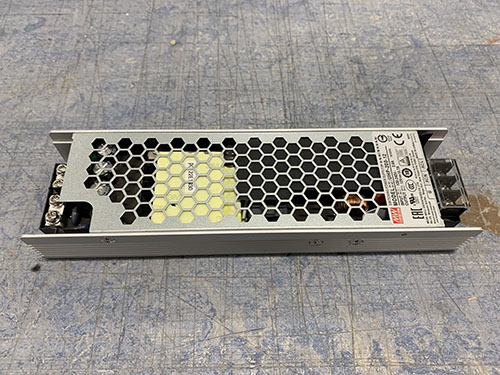
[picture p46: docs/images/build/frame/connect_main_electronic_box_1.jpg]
connect_main_electronic_box_1


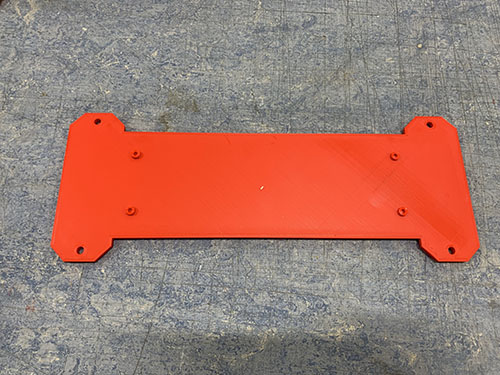
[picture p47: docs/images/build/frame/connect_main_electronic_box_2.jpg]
connect_main_electronic_box_2


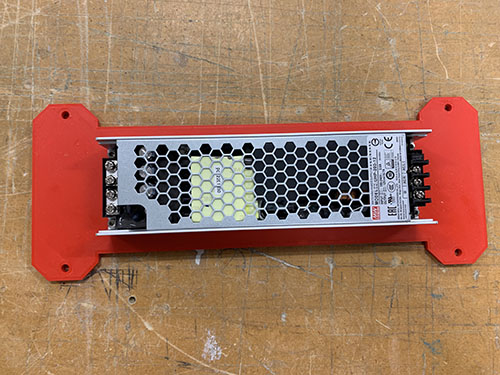
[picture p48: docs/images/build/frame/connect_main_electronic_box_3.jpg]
connect_main_electronic_box_3


The C14 connector/terminal (**E14**) and the emergency stop switch (**E17**) were inserted into the holes on the front plate of the large electronic box. 

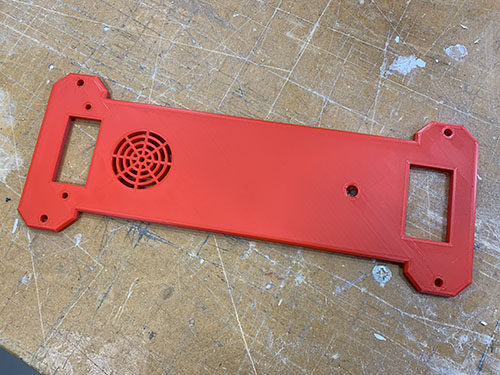
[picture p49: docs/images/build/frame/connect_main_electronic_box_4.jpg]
connect_main_electronic_box_4


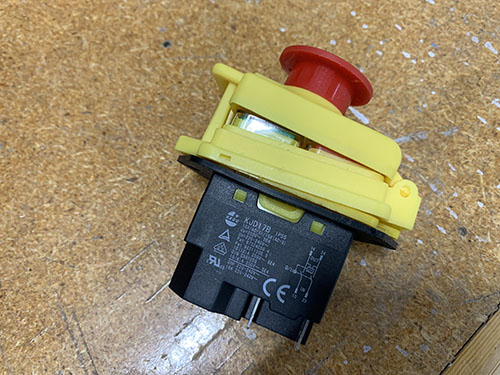
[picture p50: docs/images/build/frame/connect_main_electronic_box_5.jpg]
connect_main_electronic_box_5


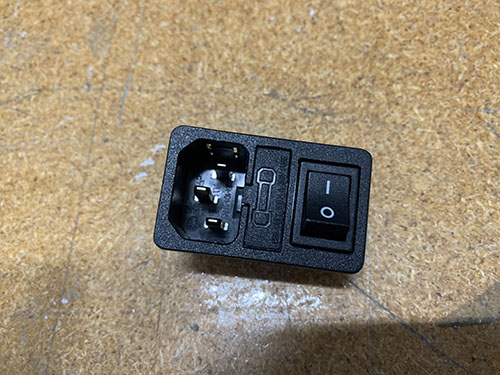
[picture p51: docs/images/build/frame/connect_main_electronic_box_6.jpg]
connect_main_electronic_box_6


A small brown/red wire (**E06**) was cut out and the ends were stripped and twisted. Two 4.8 mm spade connectors (**E26**) were then attached to the stripped wire using a plier. The space connectors were connected between **10** and **1A** on the back side of the C14 connector.

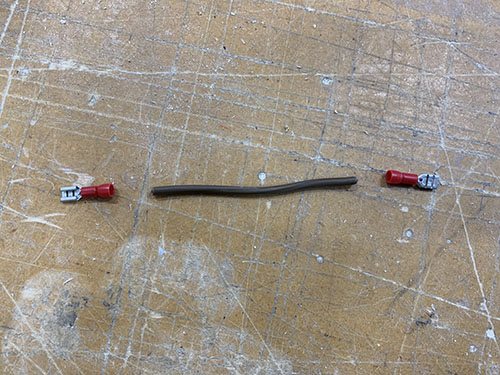
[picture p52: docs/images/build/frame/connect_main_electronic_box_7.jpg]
connect_main_electronic_box_7


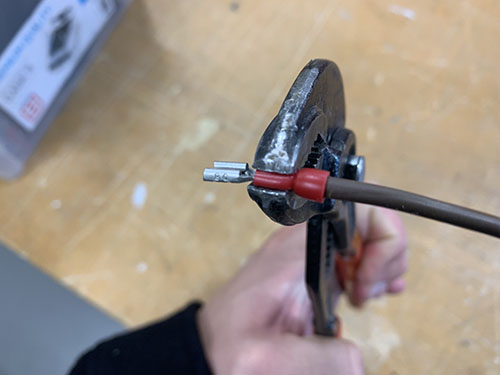
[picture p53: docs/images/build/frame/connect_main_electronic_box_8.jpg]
connect_main_electronic_box_8


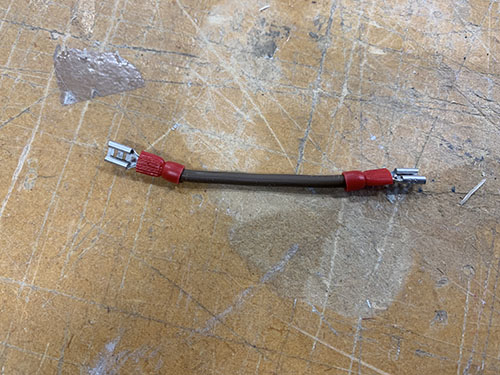
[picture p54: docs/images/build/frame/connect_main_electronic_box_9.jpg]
connect_main_electronic_box_9


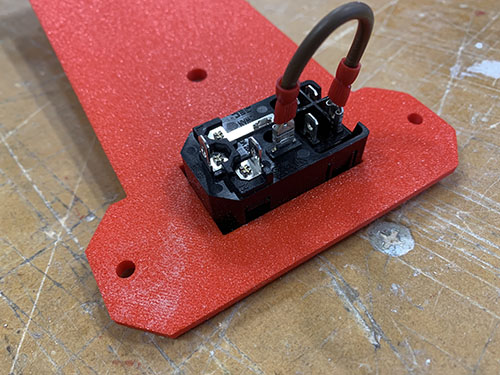
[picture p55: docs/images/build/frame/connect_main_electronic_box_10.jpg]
connect_main_electronic_box_10


A longer brown wire was cut out to reach between **L** on the C14 connector and **13** on the emergency stop switch. The ends were stripped and twisted. A 4.8 mm spade connector (**E26**) was attached to the side connected to the C14 connector and a 6.3 mm space connector (**E27**) was attached to the side connected to the emergency stop switch. The spade connectors were then connected.

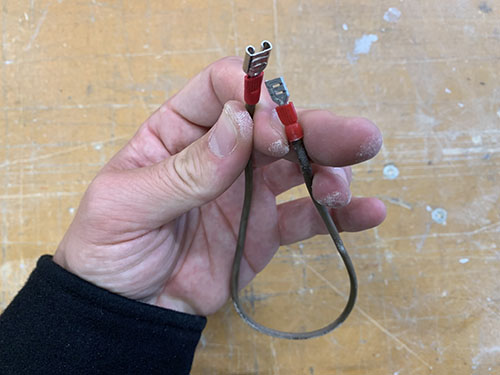
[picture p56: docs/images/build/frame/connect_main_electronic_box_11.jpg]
connect_main_electronic_box_11


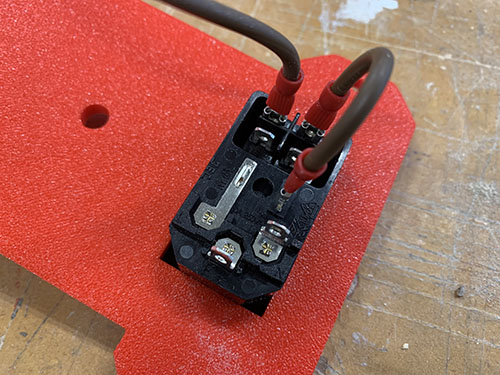
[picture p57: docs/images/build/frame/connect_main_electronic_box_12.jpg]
connect_main_electronic_box_12


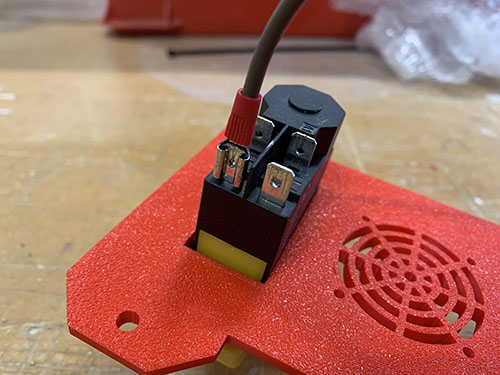
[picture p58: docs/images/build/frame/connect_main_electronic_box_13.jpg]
connect_main_electronic_box_13


Two short and one longer blue wire were cut out at an appropriate length and the ends of the wires were stripped and twisted.

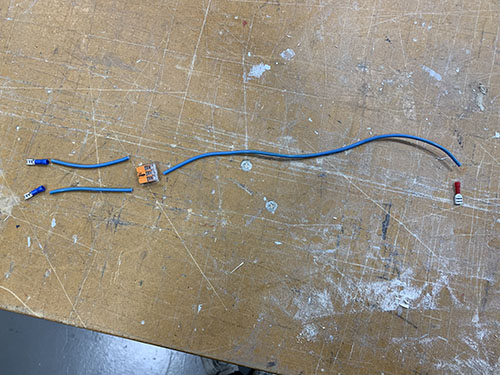
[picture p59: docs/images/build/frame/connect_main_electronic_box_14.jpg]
connect_main_electronic_box_14


Two 4.8 mm spade connector (**E26**) were attached to one of the sides of each shorter wire and the other sides were inserted and locked into 1x 3-way Wago 221-413 (**E07**).

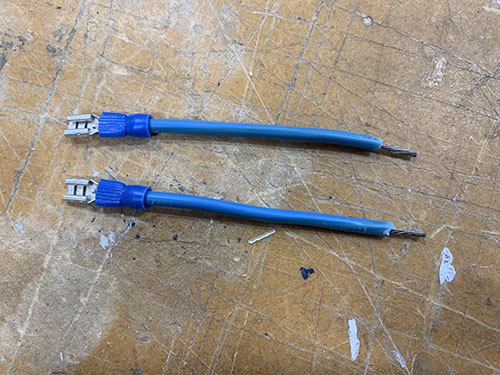
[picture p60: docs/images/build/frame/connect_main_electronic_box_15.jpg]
connect_main_electronic_box_15


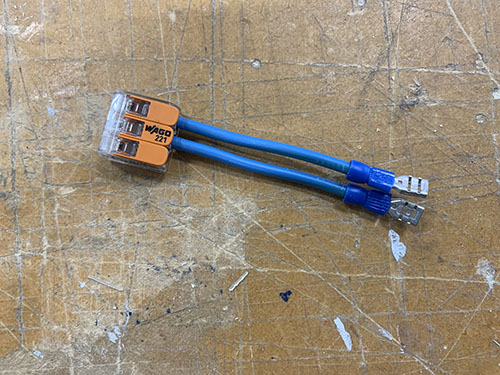
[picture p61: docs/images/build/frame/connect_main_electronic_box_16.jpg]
connect_main_electronic_box_16


A 6.3 mm space connector (**E27**) was attached to one side of the longer blue wire and the other side were inserted and locked into the 3-way Wago 221-413 (**E07**).

I didn't have access to matching colors of all the spade connectors, so I followed the appropriate color scheme of the wires instead. So please ignore if there's a mismatch between the wire color and the spade connector color in the upcoming images.

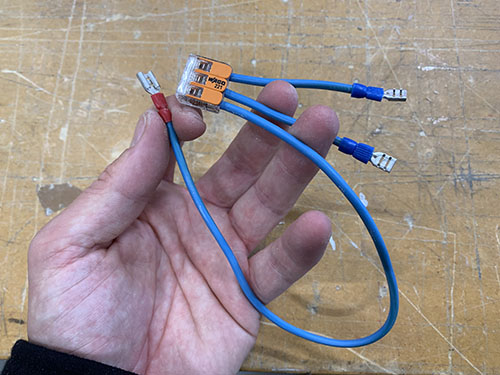
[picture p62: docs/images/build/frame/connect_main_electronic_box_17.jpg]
connect_main_electronic_box_17


The shorter blue wires were connected to **N** and **XX** on the C14 connector. The longer blue wire was connected to **23** on the emergency stop switch.

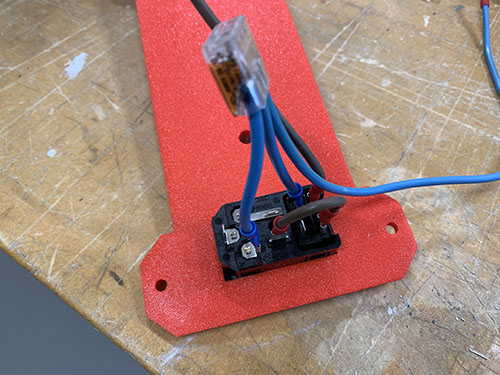
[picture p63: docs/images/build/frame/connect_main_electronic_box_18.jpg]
connect_main_electronic_box_18


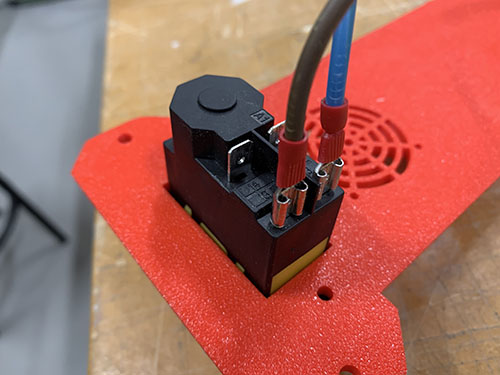
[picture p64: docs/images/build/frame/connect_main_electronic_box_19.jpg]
connect_main_electronic_box_19


One brown and one blue wire were cut out to reach between the emergency stop switch and the power supply's input terminals. The ends of the wires were stripped and twisted. Two 6.3 mm space connectors (**E27**) were attached to one side of the wires and 2x M4 ring terminals (**E24**) were attached to the other side. The blue wire's spade connector was connected to **24** on the emergency stop switch. The brown wire's spade connector was connected to **14** on the emergency stop switch.

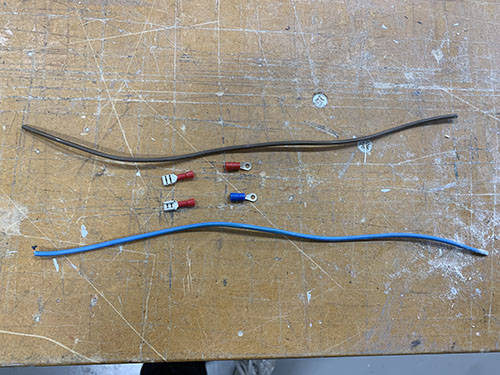
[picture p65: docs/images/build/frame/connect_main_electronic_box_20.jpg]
connect_main_electronic_box_20


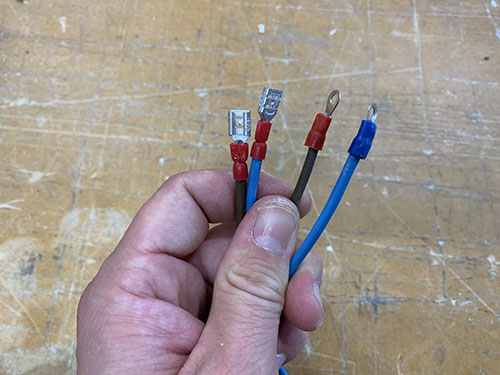
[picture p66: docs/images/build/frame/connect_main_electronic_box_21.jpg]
connect_main_electronic_box_21


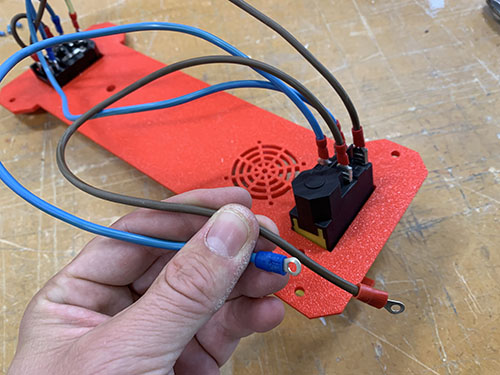
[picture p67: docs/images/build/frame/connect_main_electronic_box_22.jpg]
connect_main_electronic_box_22


A small green/yellow wire was cut out to reach between the C14 connector and the power supply's input terminals. The end of the wire was stripped and twisted, a 4.8 mm spade connector (**E26**) was attached to one side and 1x M4 ring terminal (**E24**) was attached to the other side. The spade connector was then attached to **⏚** (ground) on the C14 connector.

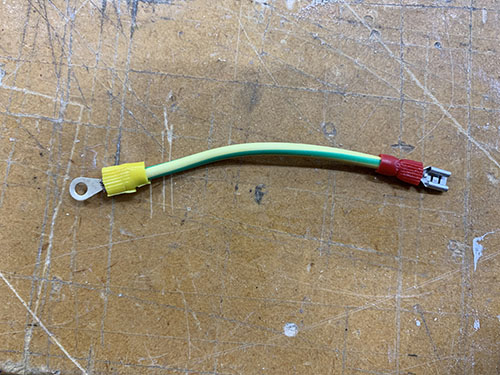
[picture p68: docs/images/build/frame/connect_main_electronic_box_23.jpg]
connect_main_electronic_box_23


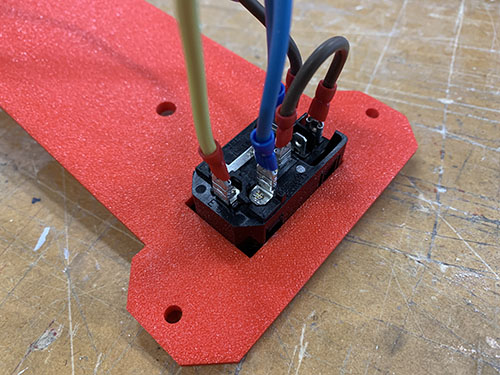
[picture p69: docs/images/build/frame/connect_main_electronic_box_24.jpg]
connect_main_electronic_box_24


The three M4 ring terminals were then connected to the power supply's input terminals in the following way:

* Brown -> AC/L
* Blue -> AC/N
* Green/Yellow -> **⏚** (ground)

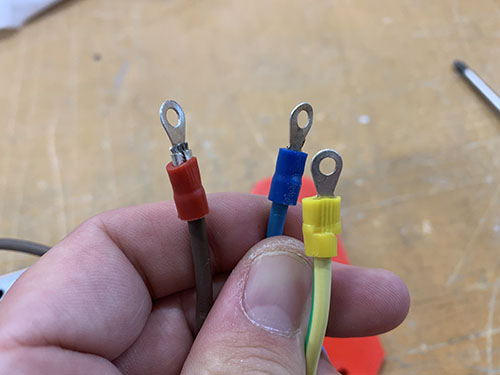
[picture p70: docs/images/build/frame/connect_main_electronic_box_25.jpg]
connect_main_electronic_box_25


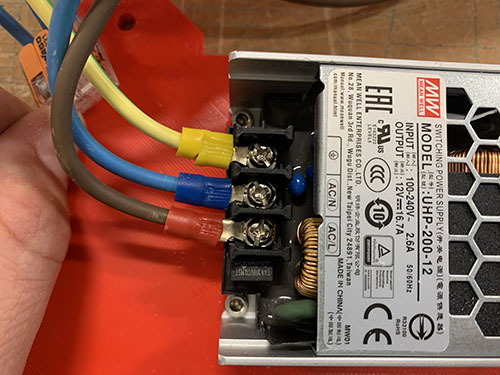
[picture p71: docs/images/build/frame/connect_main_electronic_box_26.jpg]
connect_main_electronic_box_26


Power was connected to the C14 connector (read [this](#connect-main-electronic-box) note before connecting the power) and a multimeter was used to verify that the power supply outputted 12V. The multimeter was also used to verify that the C14 connector worked properly (cut power when using the switch) and that the emergency stop switch worked propertly (cut power when pushed. Also that the emegency stop switch remains off when C14 connector is switched off and on again).

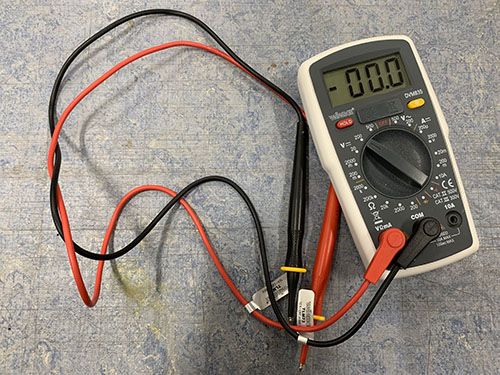
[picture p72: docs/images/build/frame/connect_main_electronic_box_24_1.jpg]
connect_main_electronic_box_26


The emergency stop switch was attached to the front plate using 2x 18mm M4 screws (**S09**), 2x M4 nuts (**N01**) and two (9 mm, 4.5 mm, 1 mm) washers (**W07**).

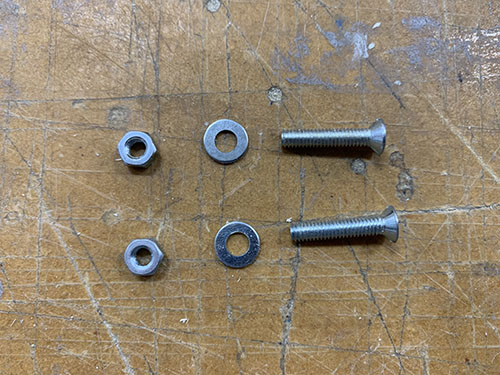
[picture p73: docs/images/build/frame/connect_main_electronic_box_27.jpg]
connect_main_electronic_box_27


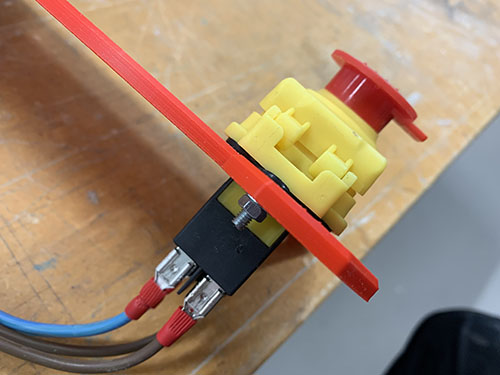
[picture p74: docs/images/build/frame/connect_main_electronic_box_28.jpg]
connect_main_electronic_box_28


The C14 connector was attached to the front plate using super glue. A cloth was used to remove excess glue.

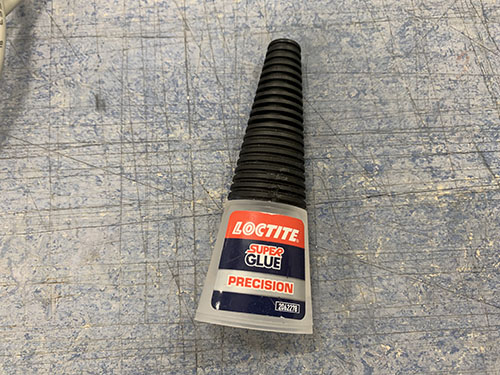
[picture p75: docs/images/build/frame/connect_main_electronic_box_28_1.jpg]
connect_main_electronic_box_28_1


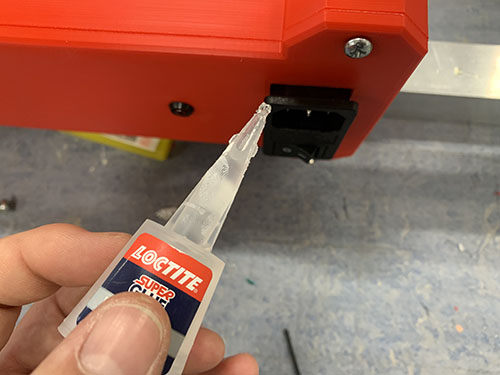
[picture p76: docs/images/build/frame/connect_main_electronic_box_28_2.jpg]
connect_main_electronic_box_28_2


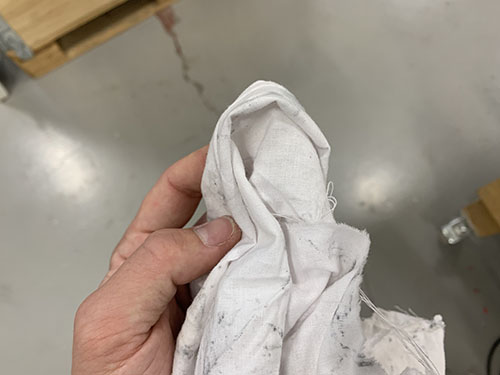
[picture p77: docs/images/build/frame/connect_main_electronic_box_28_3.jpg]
connect_main_electronic_box_28_3


Shrink tubes (**O24**) were cut out at an appropriate length, one for each spade connector. Each spade connector was then temporarily removed and inserted into its shrink tube, before attached back again. The shrink tubes were then shrunk around all the spade connectors.

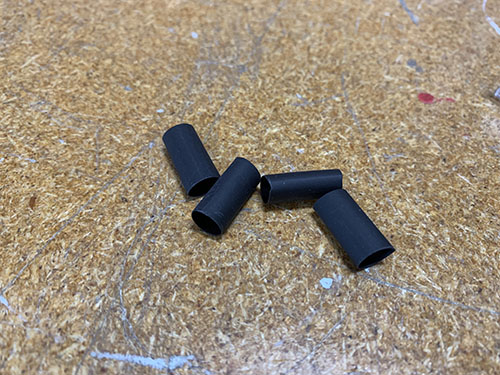
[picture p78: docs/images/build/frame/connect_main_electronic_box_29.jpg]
connect_main_electronic_box_29


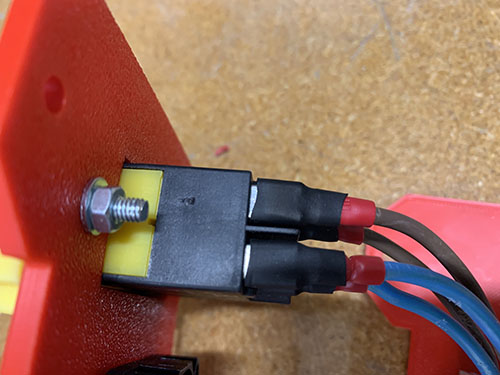
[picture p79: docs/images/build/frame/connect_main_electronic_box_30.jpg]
connect_main_electronic_box_30


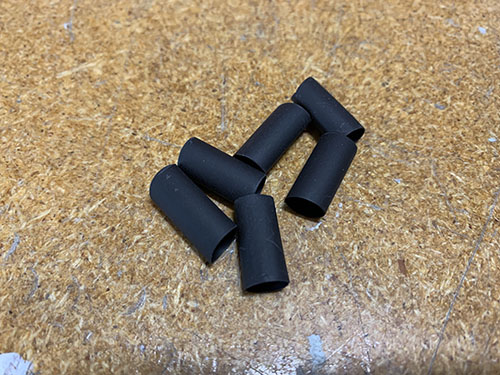
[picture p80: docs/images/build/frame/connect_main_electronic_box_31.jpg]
connect_main_electronic_box_31


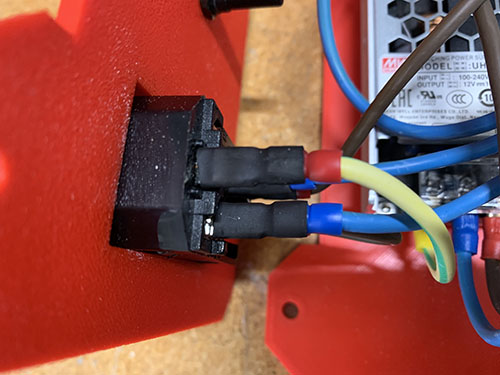
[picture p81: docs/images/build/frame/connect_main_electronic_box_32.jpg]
connect_main_electronic_box_32


## Prepare power to steppers and connect fans and LED

To prepare the power for the stepper motors, one black and one red wire (**E03**) were cut out (approx. 300 mm long) to reach between the 12V terminals on the power supply and the small electronic box containing the Arduino and CNC shield. One side of each wire was then stripped and twisted, and 2x M3 ring terminals (**E23**) were attached. 

The red wire was connected to the **V+** and the black wire was connected to **V-**.

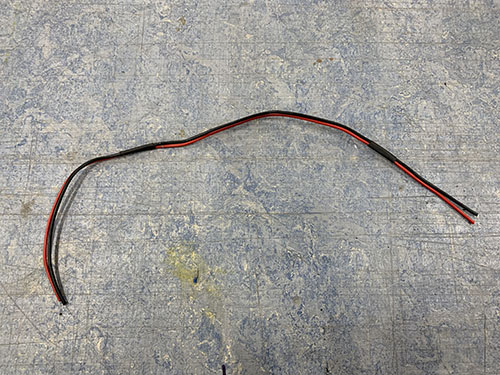
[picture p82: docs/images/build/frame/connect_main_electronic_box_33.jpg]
connect_main_electronic_box_33


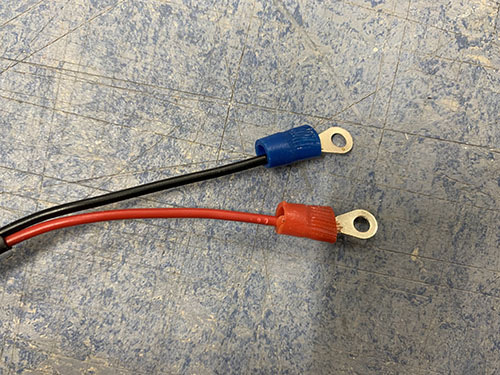
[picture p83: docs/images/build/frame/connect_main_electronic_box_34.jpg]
connect_main_electronic_box_34


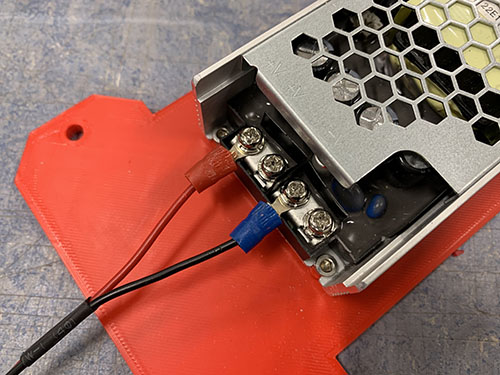
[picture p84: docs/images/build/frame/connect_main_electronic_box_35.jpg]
connect_main_electronic_box_35


A 40x40 mm 12V fan (**E01**) was attached to the back side of the large electronic box's front panel, using 4x 12 mm M3 screws (**S02**). The fan was attached to blow air out of the box.

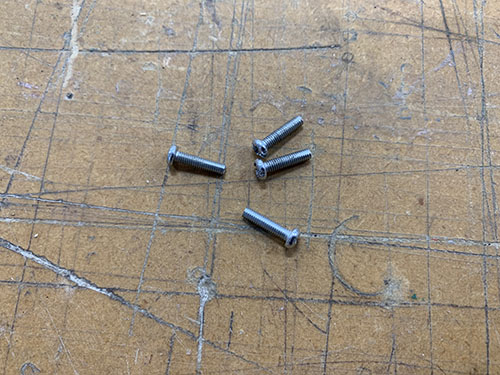
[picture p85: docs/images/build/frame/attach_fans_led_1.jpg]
attach_fans_led_1


attach_fans_led_2

attach_fans_led_3

A 12V red LED (**E22**) was inserted into the small 
~8 mm hole on the front of the large electronic box's front panel.

attach_fans_led_4

attach_fans_led_5

attach_fans_led_6

The second 40x40 mm 12V fan (**E01**) was attached to the back side of the small electronic box's front panel, using 4x 12 mm M3 screws (**S02**). A short flexible conduit (**O13**) reaching between the two eletronic boxes was cut out and the wires from the fan were inserted through it.

attach_fans_led_7

attach_fans_led_8

attach_fans_led_9

attach_fans_led_9

The loose wires of the two fans and the LED were stripped and twisted together, black together and red together. Then all three black wires were attached into the same M3 ring terminal (**E23**) and all three red wires were attached into the same M3 ring terminal (**E23**).

attach_fans_led_10

attach_fans_led_11

attach_fans_led_11

The red wires (red ring terminal) were finally connected to the **V+** and the black wires (blue ring terminal) were connected to **V-** on the 12V power supply.

attach_fans_led_13

The red and black 12V power wires intended for the stepper motors were inserted through the same short flexible conduit as the fan wires.

attach_fans_led_14

2x 3d-printed strain relief halves (**P11**) were inserted into the hole on the side of the large electronic box facing the small electronic box. The large box was then carefully closed and attached to the upper and lower frame again. It's really important that you don't have to force it closed. If that's the case you need to move some cables for it to close smoothly.

attach_fans_led_15

attach_fans_led_16

attach_fans_led_17

attach_fans_led_18

## Assemble stepper motor drivers and tune VRef

One small heatsink was attached to each DRV8825 stepper driver (**E16**).

vref_stepper_drivers_1

vref_stepper_drivers_2

Before the stepper motors were connected to the CNC shield, the stepper motor drivers' VRef needed to be tuned. The VRef regulates the voltage from the stepper driver to the stepper motor. If the VRefs are set to high, it can damage the stepper motors by supplying to much voltage.

The CNC shield (**E10**) was first attached to the Arduino Uno (**E09**).

vref_stepper_drivers_3

vref_stepper_drivers_4

The four stepper drivers were then attached to the CNC shield, one for each axis (X, Y, Z) and one for the mirrored Y-axis (A). The stepper drivers were inserted so that the "EN" pins on the stepper drivers aligned with the EN female terminal on the CNC shield.

vref_stepper_drivers_5

vref_stepper_drivers_6

vref_stepper_drivers_7

A USB cable (**E28**) was connected to the Arduino Uno and to a computer to supply the Arduino with power. 

The power wires connected to the 12v power supply were connected to the CNC shield:

* Red cable -> **+**
* Black cable -> **-**

Power was then added to the system by inserting the C13 cable (**E30**) into the C14 connector on the front panel of the large electronic box.

vref_stepper_drivers_8

A multimeter was then used to regulate the VRef on each stepper driver. The equation to calculate the VRef differs depending on the stepper driver. The DRV8825 stepper drivers are using the following equation:

vref_stepper_drivers_8_1

By checking the `I_{max}` in the technical specification for each stepper motor, the following VRefs were calculated for each stepper driver:

| Stepper driver  | I_{max} | VRef |
|---|---|---|
| X | 1.68A | 1.68/2 = 0.84V |
| Y | 1.68A | 1.68/2 = 0.84V |
| A (mirrored Y)  | 1.68A | 1.68/2 = 0.84V |
| Z | 1.68A | 1.68/2 = 0.84V |

To measure the VRef of each stepper driver, the red test probe was connected to the screw on top of the stepper driver, and the black test probe was connected to the second bottom left pin (GND). The screw was then rotated to adjust the VRef to the appropriate voltage (~0.84V).

vref_stepper_drivers_9

vref_stepper_drivers_10

## Attach Arduino and solder USB cable

The CNC shield was removed from the Arduino and the Arduino was attached to the back plate of the small electronic box using the 4x 5mm M3 screws (**S07**) unscrewed from the geared stepper motors. The USB cable was left inserted in the Arduino, as there was no space to insert it afterwards.

arduino_and_usb_1

arduino_and_usb_2

arduino_and_usb_3

The end of the USB cable was cut and stripped, showing the following 4 wires inside:

| Color | Type |
|---|---|
| Red | VCC (+5V) |
| White | Data - |
| Green | Data + |
| Black | GND |

Each wire was stripped and twisted.

arduino_and_usb_3_1

A female USB-A (**E29**) was inserted into the front plate of the small electronic box. By using a soldering iron, solder/filler metal was first added to each pin on the female USB-A before attaching the wires, to simplify the soldering. 

arduino_and_usb_4

arduino_and_usb_4

4 small shrink tubes (**O24**) were cut out and the wires were inserted into the shrink tubes. 

arduino_and_usb_7

arduino_and_usb_8

To know which wire to solder to which pin, the following schema was used. The schema illustrates when looking straight into the female USB-A, with the flat surface at the top and the internal USB pins pointing downwards. As the pins goes straight through the connector, it's possible to map it to the pins on the back.

arduino_and_usb_6_1

arduino_and_usb_6

When the correct pin-wire-mapping was found, the wires were soldered one by one, by placing the stripped wires on the pins and then pressing the solder iron onto the tip of the wires. As filler metal had already been applied to the pins, no extra filler metal had to be added. The shrink tubes were then shrunk around the wires.

arduino_and_usb_9

arduino_and_usb_10

Finally, a 3d-printed block (**P33**) was glued to the female USB-A connector and the back of the front panel to lock it into place.

arduino_and_usb_11

arduino_and_usb_12

arduino_and_usb_13

arduino_and_usb_14

## Stepper and end-stop cable management to small electronic box

The CNC shield was attached to the Arduino and 6x 3d-printed strain relief halves (**P11**) were inserted into the holes on the sides of the small electronic box.

steppers_to_cnc_shield_1

steppers_to_cnc_shield_2

Two flexible conduits (**O13**) were cut out to reach between the end of the Y-axis cable chain and the two holes in the small box. A hole was then drilled in the upper flexible conduit for the Y-axis end-stop wires to enter. To do this, the upper flexible conduit was placed where it was intended to be and tape was used to indicate the position of the hole. 

A drill was then used to create the hole in the upper flexible conduit.

steppers_to_cnc_shield_3

steppers_to_cnc_shield_4

steppers_to_cnc_shield_5

steppers_to_cnc_shield_6

The Y-axis end-stop (+ and -) wires were inserted into the hole, followed by half of the wires coming from the Y-axis cable chain. The rest of the wires were inserted into the lower flexible conduit.

To simplify the process, the cables going into the same conduit were taped together.

steppers_to_cnc_shield_7

steppers_to_cnc_shield_8

steppers_to_cnc_shield_9

The end of the conduits were then placed between the strain relief halves and the front-middle part of the box were carefully attached to the frame again, locking the strain reliefs and the flexible conduits in place.

steppers_to_cnc_shield_10

steppers_to_cnc_shield_11

## Connect steppers to CNC shield

To keep a good structure of the wires inside the small box, electrical crimp sleeves (**E15**) and contact housings (**E13**) were used. This also reduced the risks of shortings and loose wires.

steppers_to_cnc_shield_13

steppers_to_cnc_shield_18

For each stepper, the wires were cut at an appropriate length to reach to its connection on the CNC shield. Each wire were stripped and twisted. An AWG22/24 crimp connector was then attached to the end of each wire using a crimping tool. A shrinking tube (**O24**) was shrunk around the wires to keep a good structure.

The wires were then inserted and locked into a 1X4 contact housing (**E13**). Make sure to insert the wires in the correct orinentation, as the crimp connector has a "lock" that interlocks with the contact housing.

To know in which order to insert the wires, check the technical specification of your steppers. You should find something like this (given that you've bought bi-polar stepper motors):

| A+ | A- | B+  | B- |
|---|---|-----|---|
| Black | Green | Red | Blue |

**A** and **B** indicate the two different coils in the stepper motor and the colors are the colors of the wires. You want to connect the crimp connectors so that each coil's wires are next to each other: **A A B B**.

steppers_to_cnc_shield_12

steppers_to_cnc_shield_14

steppers_to_cnc_shield_15

steppers_to_cnc_shield_16

steppers_to_cnc_shield_17

steppers_to_cnc_shield_19

This was done for all four steppers (X, Y, Z, A (mirrored Y)). Tape and a sharpie was used to indicate which contact housing beloning to which stepper. The contact housings were then connected to its connections on the CNC shield.

Note that if any of the steppers are moving in the "wrong" direction later on, you can just turn the connection 180 degrees and it will move the opposite way.

steppers_to_cnc_shield_20

steppers_to_cnc_shield_21

Finally, two jumpers (**E19**) were attached to the blue and yellow column on the "Y row". This tells the Arduino to mirror the Y-stepper instructions to the stepper connected to the **A** connection.

steppers_to_cnc_shield_22

steppers_to_cnc_shield_23

## Connect end-stops to CNC shield

As with the stepper motor wires, electrical crimp connectors were used to keep a good structure in the small electornic box.

For each end-stop, the two wires were cut at an appropriate length to reach to its connection on the CNC shield. Each wire were stripped and twisted. An AWG22/24 crimp connector (**E15**) was then attached to the end of each wire using a crimping tool. 

endstops_to_cnc_shield_1

endstops_to_cnc_shield_2

As I didn't have access to any 1x2 contact housings (**E12**), a shrinking tube (**O24**) was shrunk around each crimp connectors to reduce the risk of shorts.

This was done for all end-stops (X+, X-, Y+, Y- and Z+). Tape and a sharpie was used to indicate which pair of wires beloning to which end-stop. The crimp connector pairs were then connected to its connections on the CNC shield.

endstops_to_cnc_shield_3

endstops_to_cnc_shield_4

endstops_to_cnc_shield_5

endstops_to_cnc_shield_6

## Set microstepping

Microstepping is a way to control the stepper motors in a smoother way and at a higher resolution, but usually at a lower speed and torque. 

The 6 pins (M0, M1, M2) underneath each stepper driver were used to set the microstepping for each motor. By shorting the pins in certain combinations, different type of microstepping can be achieved (**0** indicates no shorting, **1** indicates shorting):

| Microstepping | M0 | M1 | M2 |
|---|----|----|----|
| Full-step | 0  | 0  | 0  |
| 1/2 | 1  | 0  | 0  |
| 1/4 | 0  | 1  | 0  |
| 1/8 | 1  | 1  | 0  |
| 1/16 | 0  | 0  | 1  |
| 1/32 | 1  | 0  | 1  |

The 4 stepper drivers were carefully removed. The microstepping was set to `1/16` for each motor by shorting the two `M2` pins using jumpers (**E19**). The stepper drivers were then carefully inserted back again.

set_microstepping_1

set_microstepping_2

## Router cable management and connect to main power supply

!!! danger
    **THIS PART INCLUDES WIRING OF HIGH VOLTAGE ELECTRICITY THAT CAN BE LETHAL IF NOT DONE PROPERLY. THE COLORS OF THE CABLES CAN VARY DEPENDING ON REGION/COUNTRY AND YOUR COMPONENTS/PINOUT NUMBERS MIGHT LOOK DIFFERENT.
      BEFORE YOU CONNECT THE POWER CORD TO THE POWER OUTLET, YOU MUST CONSULT WITH A LICENSED ELECTRICIAN TO MAKE SURE THAT EVERYTHING IS PROPERLY WIRED AND THAT IT IS IN LINE WITH YOUR LOCAL LEGISLATIONS.**

As I wanted the emergency stop switch to kill the router as well, the router cable was inserted into the small electronic box to reach the emergency stop switch in the large electronic box.

A round cable grommet (**O25**) was inserted in the left side of the small electronic box, aligned between the two main wire holes.

The center of the hole was measured and drilled using a 8.5 mm drill. The cable grommet was then inserted and super glue was used to keep it in place.

router_small_box_1

router_small_box_2

router_small_box_3

router_small_box_4

router_small_box_5

The router cable was then inserted into the cable grommet. Some ordinary soap was used to reduce the friction between the rubber cable grommet and the rubber cable.

A cable tie (**O11**) was closed around the router cable on the inside of the box as a strain relief.

router_small_box_6

router_small_box_7

router_small_box_6_1

The large electronic box was opened once more and the router cable was inserted through the flexible conduit into the large electronic box. A cable clip (**O10**) was then used to position the router cable inside the small box.

The small electronic box was then carefully closed. It's really important that you don't have to force it closed. If that's the case you need to move some cables for it to close smoothly.

router_small_box_8

router_small_box_9

router_small_box_10

router_small_box_11

The blue and brown wires going between the emergency stop switch and the 12V power supply were cut in the middle and stripped and twisted. The router cable and the wires inside were also stripped and twisted.

router_small_box_12

router_small_box_14

router_small_box_15

router_small_box_13

The three brown wires were inserted and locked into a 3-way Wago 221-413 (**E07**). The three blue wires were also inserted and locked into a 3-way Wago 221-413 (**E07**).

The large electronic box was then carefully closed once more. It's really important that you don't have to force it closed. If that's the case you need to move some cables for it to close smoothly.

router_small_box_16

router_small_box_17

router_small_box_18

## Final test of electrical wiring

The electrical wiring was tested by plugging in a C13 cable (**E30**) into the C14 socket and the C14 switch and emergency stop switch were turned on. But before this was done, I made sure that the router was turned off.

The red LED should light up, both fans should rotate and the router should rotate when turned on.

test_electrical_wiring_1

test_electrical_wiring_2

test_electrical_wiring_3

test_electrical_wiring_4

test_electrical_wiring_5

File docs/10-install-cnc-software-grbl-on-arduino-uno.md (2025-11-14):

## Install CNC software (grbl) on Arduino Uno

The software used in this project to control the CNC machine is called `grbl`. It's an open source and high performance g-code-parser and CNC milling controller that can run on a straight Arduino Uno. To be able to install the software on the Arduino, an external computer was needed.

### Install Arduino Software (IDE)
To be able to install `grbl` on the Arduino, `Arduino Software (IDE)` was installed on the computer. This program is used to upload code to the Arduino. The program was downloaded from Arduino's official website and the instructions were followed: 

[https://www.arduino.cc/en/software](https://www.arduino.cc/en/software)

After starting the program, you should see something like this:

install_software_1

### Install GRBL
After installing the Arduino Software, the latest stable version of `grbl` was downloaded (as zip-format) from their official GitHub release page: 

[https://github.com/gnea/grbl/releases](https://github.com/gnea/grbl/releases)

After unzipping the file, you should see something similar to this in the folder:

install_software_2

Before `grbl` was loaded into the `Arduino Software (IDE)`, a minor adjustment had to be done to `grbl's` config file, `config.h`. The reason for this was because when `gbrl` released v1.1, it changed the pin used by the Z end-stops. If this wasn't done, the Z end-stops wouldn't be recognized by `grbl`. To tell `grbl` that the old way of accessing the Z end-stops should be used, a specific variable in the `config.h` was commented out. 

The config `grbl/config.h` was opened in a text editor and the line were the variable `VARIABLE_SPINDLE` is set was commented out by adding two slashes (//) at the beginning of the line (see the last line):

```
// Enables variable spindle output voltage for different RPM values. On the Arduino Uno, the spindle
// enable pin will output 5V for maximum RPM with 256 intermediate levels and 0V when disabled.
// NOTE: IMPORTANT for Arduino Unos! When enabled, the Z-limit pin D11 and spindle enable pin D12 switch!
// The hardware PWM output on pin D11 is required for variable spindle output voltages.
// #define VARIABLE_SPINDLE // <-- THIS SHOULD BE COMMENTED OUT!!
```

The updated `config.h` was saved.

The `Arduino Software (IDE)` was then launched and the `Sketch > Include Library > Add .ZIP Library...` menu alternative was clicked:

install_software_3

You should see a pop-up similar to this:

install_software_4

The unzipped `grbl` directory was opened and the folder `grbl` was chosen. After choosing the folder, a text below the editor appeared stating `Library added to your libraries. Check "Include library" menu`.

A USB cable was connected to the USB connection on the small electronic box.

Next, connect the Arduino to your computer.

install_software_5

To let the IDE know where to upload the software, the correct serial port and board were chosen. The serial port was set under `Tools > Port > SOMETHINGSOMETHING (Arduino Uno)`. 

```
If you have trouble finding the correct port, you might need to install 
CH340 drivers. It might occurr if you're using an Arduino clone. Look at
this resource for more info: 
https://learn.sparkfun.com/tutorials/how-to-install-ch340-drivers/all
```

install_software_8

The board was set under `Tools > Board > Arduino Uno`.

install_software_8_1

To test if the correct board and serial port were chosen, the template code (default code available when launching the IDE) was compiled by clicking on the check mark in the top left corner. When the compiling was done, the right-pointing arrow was clicked to upload the code to the Arduino. If successfull, you should see a text saying `Done uploading` below the editor.

install_software_9

install_software_10

The IDE was now ready to upload `grbl` to the Arduino. This was done by clicking `File > Open` in the top menu:

install_software_11

In the pop-up window, the downloaded folder was found and the following file  `grbl/examples/grblUpload/grblUpload.ino` was opened.

install_software_12

A new pop-up was opened and the `grbl` code was compile by clicking on the check mark. When done, the compiled code was uploaded to the Arduino by clicking on the right-pointing arrow. `grbl` was now installed on the Arduino!

install_software_13

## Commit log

2025-11-14 updated image location within mkdocs directory structure
    [BRACKET.stl, CABLE_CHAIN_MOUNT.obj, CABLE_CHAIN_MOUNT.stl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]
2025-11-14 Update print statement from 'Hello' to 'Goodbye'
2025-11-14 Update and rename 10-install-cnc-software-grbl-on-arduino-uno.md to 10-software.md
